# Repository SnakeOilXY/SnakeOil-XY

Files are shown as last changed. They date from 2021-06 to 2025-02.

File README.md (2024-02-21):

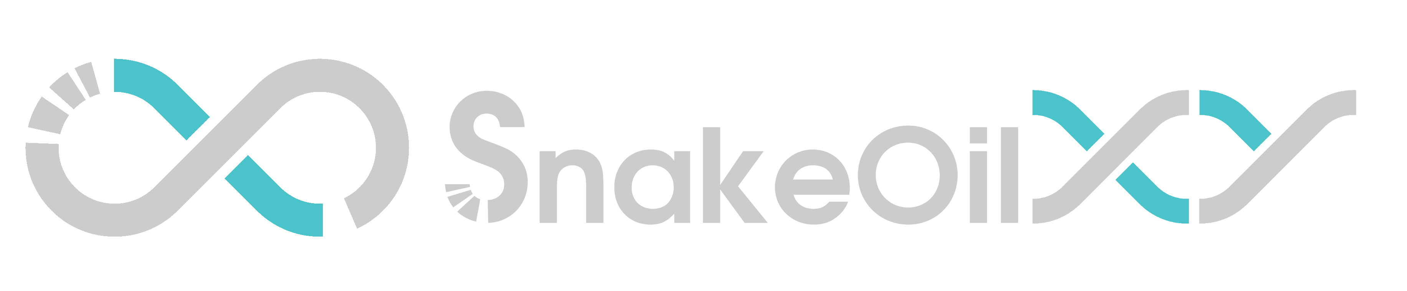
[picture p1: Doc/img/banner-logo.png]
Banner-logo


<a href="https://discord.gg/WZVP2HuAag" style="height: 40px !important;">Join us on Discord</a>

<a href='https://www.amazon.jp/hz/wishlist/ls/2AHXTCG01RYAZ?ref_=wl_share' target='_blank'>Buy Me a spool at amazon Japan</a>

# SnakeOil XY

Fully open source configurable high speed CoreXY 3D printer. Inspired by [HevORT](https://miragec79.github.io/HevORT/), [Voron](https://vorondesign.com/), [Annex Engineering](https://github.com/Annex-Engineering) and [EVA2](https://main.eva-3d.page/) design.

- Does not require any custom-machined parts or custom-cut panels.
- Can be selected one of the follwing kinematics.
    - Standard : Traditional corexy kinematic.
    - 4PR : High-performance machine with automatic squaring gantry capacity. This configuration uses custom [Extended CoreXY kinematic](https://github.com/SnakeOilXY/klipper-extended-corexy-kinematic) (Mixed cartesian and corexy).
    - IDEX : Hybrid corexy IDEX.
- CoreXY, IDEX, and Extended-CoreXY kinematics.
- Designed to last, parts under stress are embedded with long bolts to handle the load.
- And our industry-leading SnakeOil technology :3 

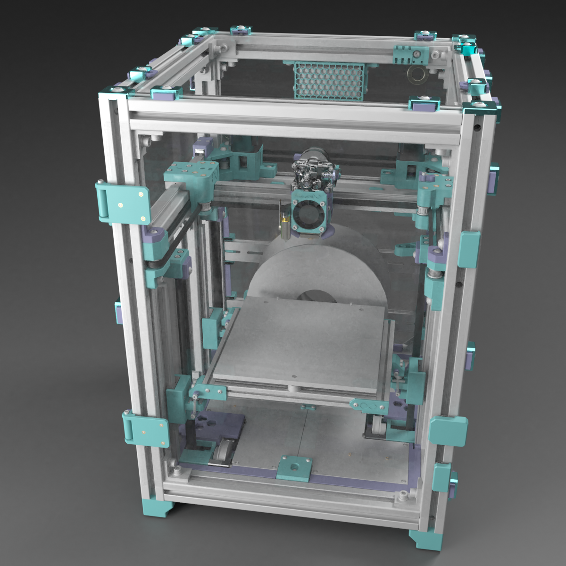
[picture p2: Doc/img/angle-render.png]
Render-angle


## Beta 3 release (2023-01-28)

- Add [IDEX variant](./BETA3_IDEX_Release_STL)(by Charles)
- Add [4PR variant](./BETA3_4PR_Release_STL) with new [Extended CoreXY kinematic](https://github.com/SnakeOilXY/klipper-extended-corexy-kinematic)
- Add klicky probe support(by Charles)
- New bed coupling kinematic using silicon spacers
- Add side-blower aux fan module
- Add EBB can toolhead board support
- Remove outdated components
- Merge toolhead design(1515 and 2020 gantry now use the same toolhead front/back/bottom design) and some small improvements on geometry

## Features

<table>
    <thead>
        <tr>
            <th>Feature</th>
            <th>Credit/Inspiration by/Description</th>
        </tr>
    </thead>
    <tbody>
        <tr>
            <td>Selectable kinematic : CoreXY, Hibryd-CoreXY </td>
            <td>Added on beta3 release</td>
        </tr>
        <tr>
            <td>Selectable single or dual toolhead </td>
            <td>Added on beta3 release</td>
        </tr>
        <tr>
            <td>3 Point auto bed tramming</td>
            <td>HevORT, Wobble ring</td>
        </tr>
        <tr>
            <td>Belted Z</td>
            <td>Lulz bot, Voron</td>
        </tr>
        <tr>
            <td>Din mounter</td>
            <td>Voron</td>
        </tr>
        <tr>
            <td>Cross belt corexy belt path</td>
            <td>HevORT</td>
        </tr>
        <tr>
            <td>Eva compatible toolhead</td>
            <td>EVA</td>
        </tr>
        <tr>
            <td>Filament spoll in side chamber</td>
            <td>-</td>
        </tr>
        <tr>
            <td>Quick release panels</td>
            <td>Added on beta2 release</td>
        </tr>
        <tr>
            <td>Built-in chamber air filter</td>
            <td>Added on beta1 release</td>
        </tr>
        <tr>
            <td>Auto build sheet detect and profile loader</td>
            <td>Work in progress</td>
        </tr>
        <tr>
            <td>AIO filament runout + jam detector + width sensor</td>
            <td>Work in progress</td>
        </tr>
        <tr>
            <td>Modular sensor add-on system</td>
            <td>Work in progress</td>
        </tr>
        <tr>
            <td>Probe(bed mesh) on print area only</td>
            <td>Added on beta2 using klipper macro</td>
        </tr>
        <tr>
            <td>Screwless belt mounter</td>
            <td>VzBot</td>
        </tr>
        <tr>
            <td>Bed fan</td>
            <td>Qholia</td>
        </tr>
    </tbody>
</table>

## Input shaper test result (beta2 1515 gantry with Sherpa mini extruder)

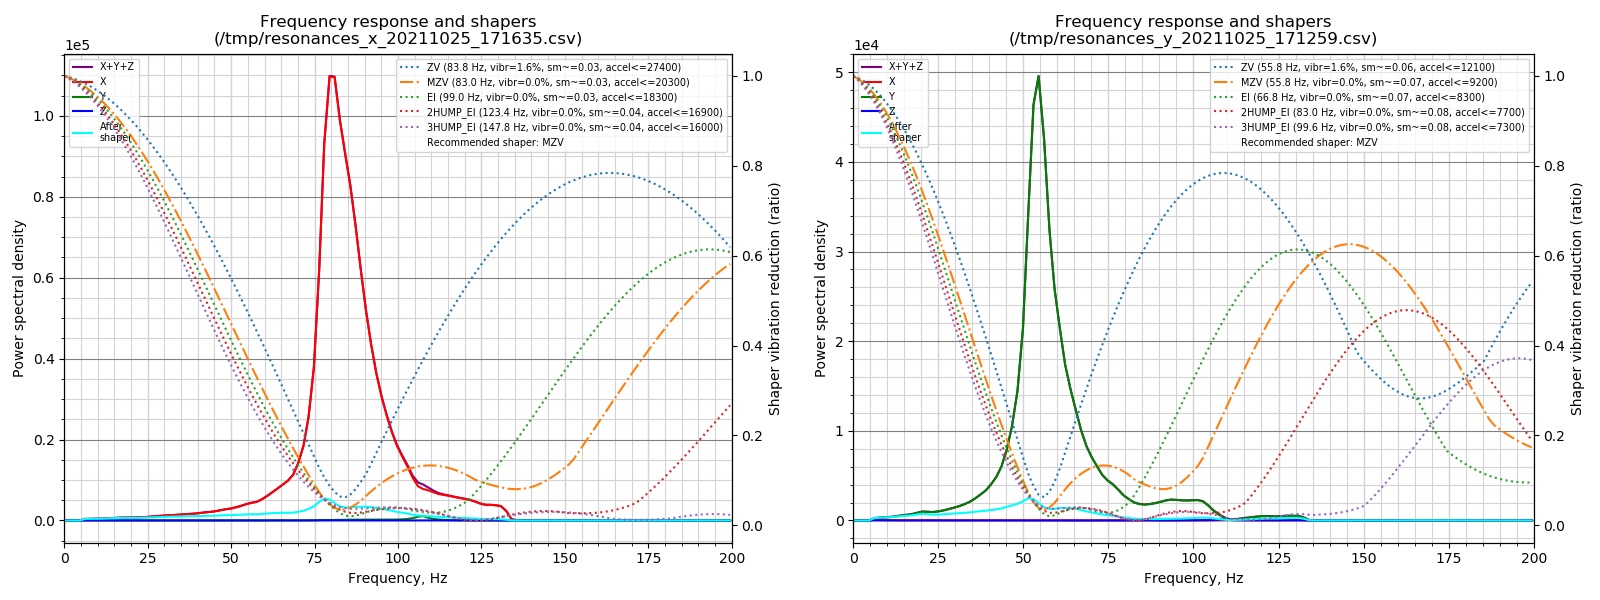
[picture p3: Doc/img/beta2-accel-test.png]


## Layer pitch measure (beta2 1515 gantry with Sherpa mini extruder)

- Measure result provided by [株式会社グーテンベルク](https://gutenberg.co.jp/)
- PLA, 0.4mm nozzle, sliced with Cura 4.12.1 using "CoreXY FAST" profile.

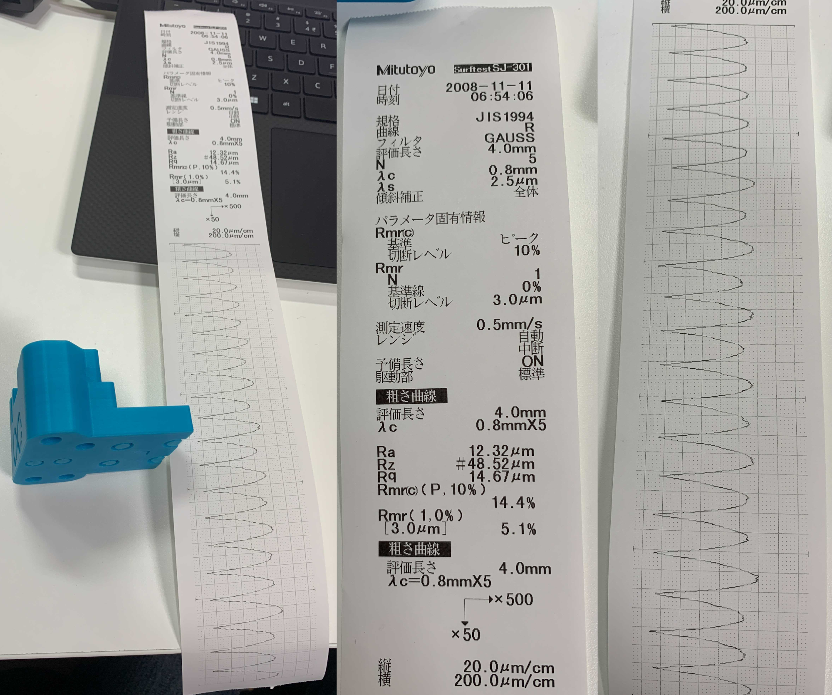
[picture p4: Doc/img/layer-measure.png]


## Demo videos

<table>
    <thead>
        <tr>
            <th></th>
            <th align="center">Bed coupling</th>
            <th align="center">SpeedBoatRace</th>
            <th align="center">Slow benchy</th>
        </tr>
    </thead>
    <tbody>
        <tr>
            <td>Video</td>
            <td align="center"><a href="https://youtu.be/pQPhEykthEg" rel="nofollow">
            Bed coupling</a></td>
            <td align="center"><a href="https://youtu.be/tPoP6zmxsCY" rel="nofollow">
            Speed benchy</a></td>
            <td align="center"><a href="https://youtu.be/kLawpgAUUPE" rel="nofollow">
            Speed benchy</a></td>
        </tr>
        <tr>
            <td>Hardware version</td>
            <td align="center">beta1</td>
            <td align="center">beta2</td>
            <td align="center">beta2</td>
        </tr>
    </tbody>
</table>

## BOM

## **_SnakeOil-XY currently has 2 versions_**

<code>Both machines are practicaly identical, only difference is the build volume. </code>

### 180x180x180mm build volume (Standard)

- [180<sup>3</sup>mm BOM](./Doc/BOM/bom-180.md)

### 250x240x230mm build volume (Large)

- [250<sup>3</sup>mm BOM](./Doc/BOM/bom-250.md)

## Manual

[>>> Click here <<<](./Doc/Manual/README.md)

## Firmware

[>>> Click here <<<](./Firmware/README.md)

## Copyright Notice

- [Sherpa mini extruder](https://github.com/Annex-Engineering/Sherpa_Mini-Extruder) is an original work of [Annex Engineering](https://github.com/Annex-Engineering), modified parts using their source code/design files are re-released under [ANNEX Engineering License](https://github.com/Annex-Engineering/ANNEX-Engineering-License-Agreement/blob/main/LICENSE.md).
- [EVA2](https://github.com/EVA-3D/eva-main) is an original work of [EVA-3D](https://github.com/EVA-3D), modified parts using their source code/design files are re-released under [GNU General Public License v3.0](https://github.com/EVA-3D/eva-main/blob/main/LICENSE)
- This printer design(SnakeOil XY), it's document and software are released under [GNU General Public License v3.0](https://github.com/ChipCE/SnakeOil-XY/blob/master/LICENSE)

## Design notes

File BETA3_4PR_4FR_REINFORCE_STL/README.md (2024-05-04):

# BETA3 Release - 4PR variant

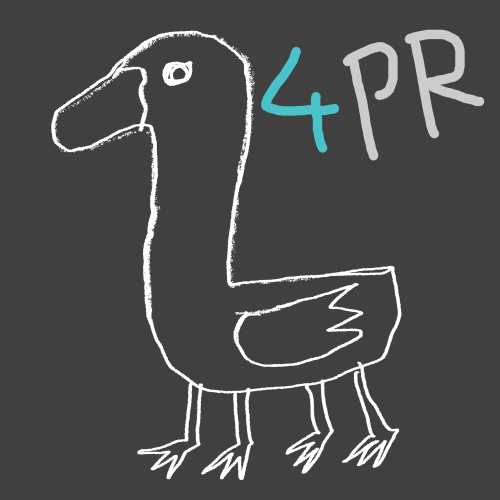
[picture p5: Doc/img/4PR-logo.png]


4PR(four paws runner) is an upgrade can add ontop of standard SnakeOilXY machines. This upgrade use our new kinematic called [Extended-corexy](https://github.com/SnakeOilXY/klipper-extended-corexy-kinematic). By adding two motors to assist the gantry on both ends, this upgrade greatly improves the performance of the existing CoreXY motion system.

## BOM

- WIP

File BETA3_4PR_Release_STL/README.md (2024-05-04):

# BETA3 Release - 4PR variant



4PR(four paws runner) is an upgrade can add ontop of standard SnakeOilXY machines. This upgrade use our new kinematic called [Extended-corexy](https://github.com/SnakeOilXY/klipper-extended-corexy-kinematic). By adding two motors to assist the gantry on both ends, this upgrade greatly improves the performance of the existing CoreXY motion system.

## BOM

<table>
    <thead>
        <tr>
            <th>Item</th>
            <th>Quantity</th>
            <th>Description</th>
            <th>default link/affiliate link</th>
            <th>non-affiliate link</th>
        </tr>
    </thead>
    <tbody>
        <tr>
            <td>M3x4-HeatSet</td>
            <td>12</td>
            <td>M3 X D4.2 X L4.0</td>
            <td><a href="https://s.click.aliexpress.com/e/_Ad1n92" rel="nofollow">Aliexpress</a></td>
            <td><a href="https://www.Aliexpress.com/item/1005002526998853.html" rel="nofollow">Aliexpress</a></td>
        </tr>
        <tr>
            <td>M4 hex nut</td>
            <td>2</td>
            <td></td>
            <td></td>
            <td></td>
        </tr>
        <tr>
            <td>Socket head M3x10</td>
            <td>8</td>
            <td>button head also works</td>
            <td>-</td>
            <td>-</td>
        </tr>
        <tr>
            <td>Socket head M3x25</td>
            <td>4</td>
            <td>button head also works</td>
            <td>-</td>
            <td>-</td>
        </tr>
        <tr>
            <td>Button head M3x12</td>
            <td>8</td>
            <td>-</td>
            <td>-</td>
            <td>-</td>
        </tr>
        <tr>
            <td>Button head M3x30</td>
            <td>8</td>
            <td>-</td>
            <td>-</td>
            <td>-</td>
        </tr>
        <tr>
            <td>Button head M5x25</td>
            <td>4</td>
            <td>-</td>
            <td>-</td>
            <td>-</td>
        </tr>
        <tr>
            <td>Button head M6x14</td>
            <td>6</td>
            <td>-</td>
            <td>-</td>
            <td>-</td>
        </tr>
        <tr>
            <td>Grub screw M5x20</td>
            <td>2</td>
            <td>-</td>
            <td>-</td>
            <td>-</td>
        </tr>
        <tr>
            <td>Nema 17 motor</td>
            <td>2</td>
            <td>Use the same type as AB motors.max length 48mm</td>
            <td>-</td>
            <td>-</td>
        </tr>
        <tr>
            <td>20T 6mm Pulley (5mm bore)</td>
            <td>2</td>
            <td>-</td>
            <td>-</td>
            <td><a href="https://www.Aliexpress.com/item/33023279793.html" rel="nofollow">Aliexpress</a></td>
        </tr>
        <tr>
            <td>20T 6mm Smooth Idler (5mm bore)</td>
            <td>2</td>
            <td>-</td>
            <td>-</td>
            <td><a href="https://www.Aliexpress.com/item/33023133633.html" rel="nofollow">Aliexpress</a></td>
        </tr>
        <tr>
            <td>20T 6mm Tooth Idler (5mm bore)</td>
            <td>4</td>
            <td>-</td>
            <td>-</td>
            <td><a href="https://www.Aliexpress.com/item/33023133633.html" rel="nofollow">Aliexpress</a></td>
        </tr>
        <tr>
            <td>MR115 bearing</td>
            <td>2</td>
            <td>-</td>
            <td>-</td>
            <td>-</td>
        </tr>
    </tbody>
</table>

## Other info

- comming soon

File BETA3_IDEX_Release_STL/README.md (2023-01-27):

# BETA2 Release(outdated document)

## What changed from Beta1

- Better 2020 gantry.
- New option for 1515 gantry with huge performance boost(see shaper test result below).
- New option for 1515 bed frame.
- New Z rail block mounting with limiter by default. This will keep the bed from tilting too much that cause the z probe cannot reach the bed.
- Better sherpa mini extruder mounter with 16mm shorter filament path.
- Added quick release front door and panel mounts.

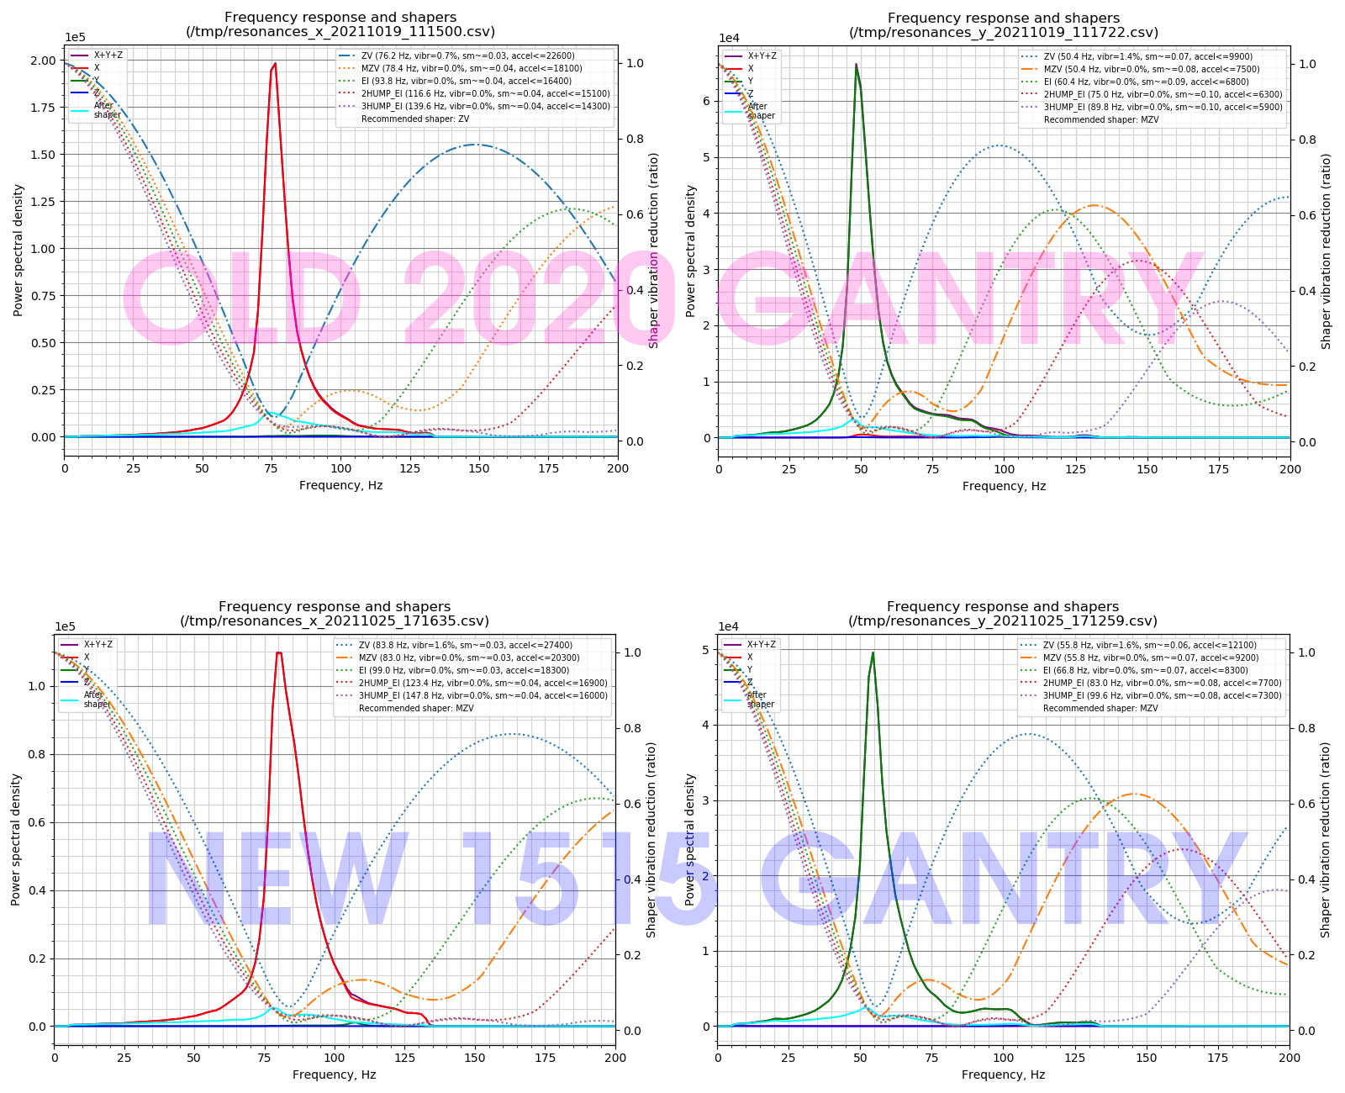
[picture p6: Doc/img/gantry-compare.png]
Banner


## What you need to reprint if you already have beta1 parts

- Z block mount
  - <code>1x_z-rail-block-mount-right-with-limiter.stl</code>
  - <code>2x_z-rail-block-mount-left-with-limiter.stl</code>
- Y carrier
  - <code>1x_y-carrier-bottom-left.stl</code>
  - <code>1x_y-carrier-bottom-right.stl</code>
  - <code>1x_y-carrier-top-left.stl</code>
  - <code>1x_y-carrier-top-right.stl</code>
- Extruder carrier parts
  - <code>1x_extruder-cable-support.stl</code>
  - <code>2x_extruder-belt-clamp.stl</code>
  - <code>2x_extruder-belt-tesioner.stl</code>
  - <code>1x_extruder-back-plate.stl</code>
  - <code>1x_extruder-front-plate.stl</code>
  - <code>And Sherpa mini mounter parts</code>

## What will be keep/change/added on later stable release

- Parts are tested and will not change on stable release
  - Motion system (XYZ) axis parts
  - Toolhead parts
  - Back and bottom panels/electronics mounter
- Parts are not tested, might change on later release
  - None
- Parts will be added later
  - Parts for 250mm3 machine size
  - Neopixel mount
  - Mounter to feed filament from outside enclosure
  - AIO filament sensor(jam/runout/fil.width detect)
  - Nozzle brush
- Parts will be replaced
  - None

## Parts printing

- Material : PETG, ABS, PC or anything you think will withstand the chamber temp you need.

- Recommended slicer setting:
  - Layer height : 0.2mm
  - Wall lines count : 5
  - Top/Bottom layers : 5
  - Infill : Gyroid 30%
  - Support placement : Touching d plate only

## Assembly, build help and bug report

- I don't have enough time to make the document atm. I will try to add document and build manual after finished design all the incomplete machine parts.
- For build log, help, and bug report please using [Our discord server](https://discord.gg/WZVP2HuAag)

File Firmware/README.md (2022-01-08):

# firmware

## Which firmware can be used

- Marlin
- Klipper
- RRF

## What does the board need that it can be used?

- 32bit
- 6 Stepper Motors or 5 Stepper + 1 Toolboard
- Neopixel Support
- 3 Thermistor Inputs (Hotend, Heated Bed, Enclosure)
- min 3 fan outputs

## Some Boards to choose from (incomplete list)

- Fysetc Spider
- BTT Octopus
- Mellow Fly Board
- BTT E3 RFF + IDEX
- BTT SKR Pro
- SKR 2.0 + BTT Mot Exp
- Duet 3 Mini 5+ + 2+ Addon or + Toolboard
- Duet 3
- Fysetc S6

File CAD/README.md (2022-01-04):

# CAD files

## FreeCAD source files

- You will need [FreeCAD](https://www.freecadweb.org/) and additional plugins to open the CAD file.
- After installed FreeCAD open menu <code>Tools</code> -> <code>Addon manager</code> then install <code>Assembly4</code> and <code>Fasteners</code> plugin.

## STEP

- There is no requirement to open STEP file, but the file is quite big and might take a long time to load

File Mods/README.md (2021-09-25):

# Some Mods for the SOXY
* GE5C Mod for the Bed (Voron Trident Inspired)

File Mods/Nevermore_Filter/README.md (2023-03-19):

# Nevermore Micro Mount for SnakeOil-XY

## Overview

This mod uses a custom plenum that mounts from the bottom (in stead of the side). I've been using it for roughly 100+ hours and have had zero issues so far. It's made a huge difference in the ABS fumes, and I also saw an increase in chamber temps by about ~5-7C.

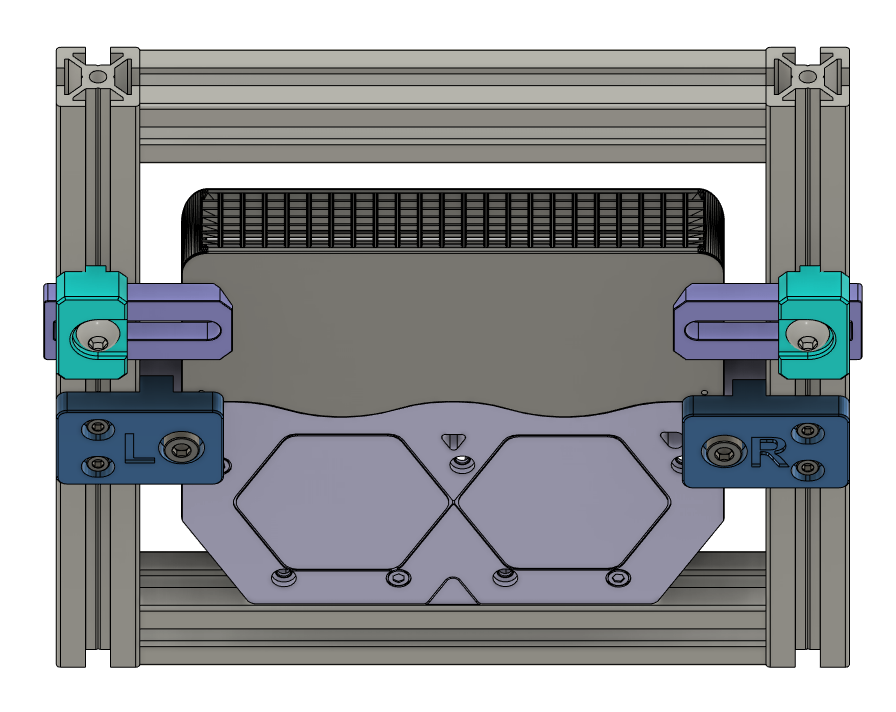
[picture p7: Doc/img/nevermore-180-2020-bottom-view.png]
Nevermore


Currently supports:
  - 180 size
    - 2020 bed - tested ✅
    - 1515 bed - untested ❓
  - 250 size 1515 bed - untested ❓
    - Can mount forward-facing, or sideways (potentially fitting 2x filters!)
  - IDEX 1515 bed - untested ❓
    - Easily fits 2x filters

## Printed parts

You will need to print the following parts:
  - **Custom Nevermore plenum**
    - Same for all sizes, except the 250 sideways mount for fitting 2x filters back-to-back
  - **Left and right mounts** inside their respective directories
  - **Center brace** (IDEX only)
  - **Nevermore cartridge**
    - You can use any Nevermore cartridge that you like, but I've supplied a custom cartridge that faces downward **and** uses the slide-in magnets. This worked the best for my use-case.
  - **[Optional] cartridge supports** to prevent cartridge from falling during printing (180 size 2020 bed only)
  - **[Optional] 1515 adapter** to support plenum against the back 1515 extrusion (originally designed to fit 2020 slot)

## BOM

In addition to the standard [Nevermore Micro BOM](https://github.com/nevermore3d/Nevermore_Micro#bom-v5), you will also need:

Fasteners (2020 bed)
  - 2x M5x7Dx7L heat set inserts
  - 2x M5x10mm socket head screws
  - 4x M3x8mm socket head screws
  - 4x M3 2020 T-nut
  - [optional] 1x M5x12mm button head screw and T-nut for each optional cartridge support arm

Fasteners (1515 bed)
  - 2x M5x7Dx7L heat set inserts
  - 2x M5x10mm socket head screws
  - 4x M3x12mm socket head screws
  - 4x M3 hex nut
  - [optional] 3x M3x6mm socket head screws (for rear 1515 support adapter)

Fasteners (IDEX 1515 bed 2x filters)
  - 2x M5x7Dx7L heat set inserts
  - 4x M5x10mm socket head screws
  - 4x M3x12mm socket head screws
  - 4x M3 hex nut

See each directory for more info.

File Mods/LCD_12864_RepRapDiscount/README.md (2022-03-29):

# RepRapDiscount Full Graphic Smart Controller (128x64 ST7920)

This type of LCD screen is often used in older Chinese 3D printers. This model would be useful for those who cannibalize old printers to build SnakeOil-XY. Silkscreen reads like: "RepRapDiscount Full Graphic Smart Controller www.bigtree-tech.com".

LCD controller: ST7920

[printer.cfg sample](sample-printer-cfg.cfg) - you can replace the latter part with the pin arrangement of your MCU.

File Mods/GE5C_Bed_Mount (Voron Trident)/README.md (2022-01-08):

# WORK IN PROGRESS
## Not tested Yet

BOM (different from the mainline repo)

* 9x M3x6 DIN 7380 Screw
* 6x M5x16 DIN 7380 Screw
* 3x M5 Nut
* 3x GE5C Bearing or IGUS EGLM-05

The Nut has to be inserted while printing via a Pause command.

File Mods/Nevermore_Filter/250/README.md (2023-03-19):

# Nevermore mount for SnakeOil-XY 250 **(UNTESTED)**

There are two options for the 250 version
- Forward-facing 
- Sideways-facing, which potentially allows for installing two filters

The STEP file includes both versions (one of them mirrored)

## Forward-facing **(UNTESTED)**
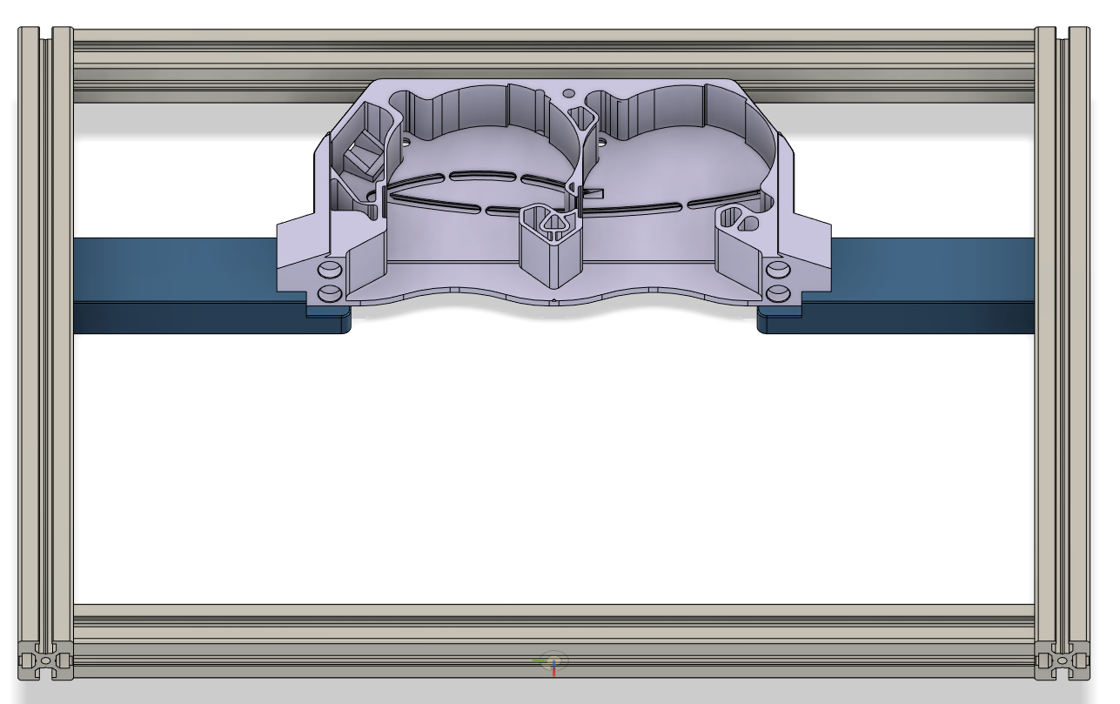
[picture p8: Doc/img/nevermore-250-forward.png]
nevermore-250-forward


I've also included and optional 1515 plenum support adapter (forward-facing only), but it may not be necessary.

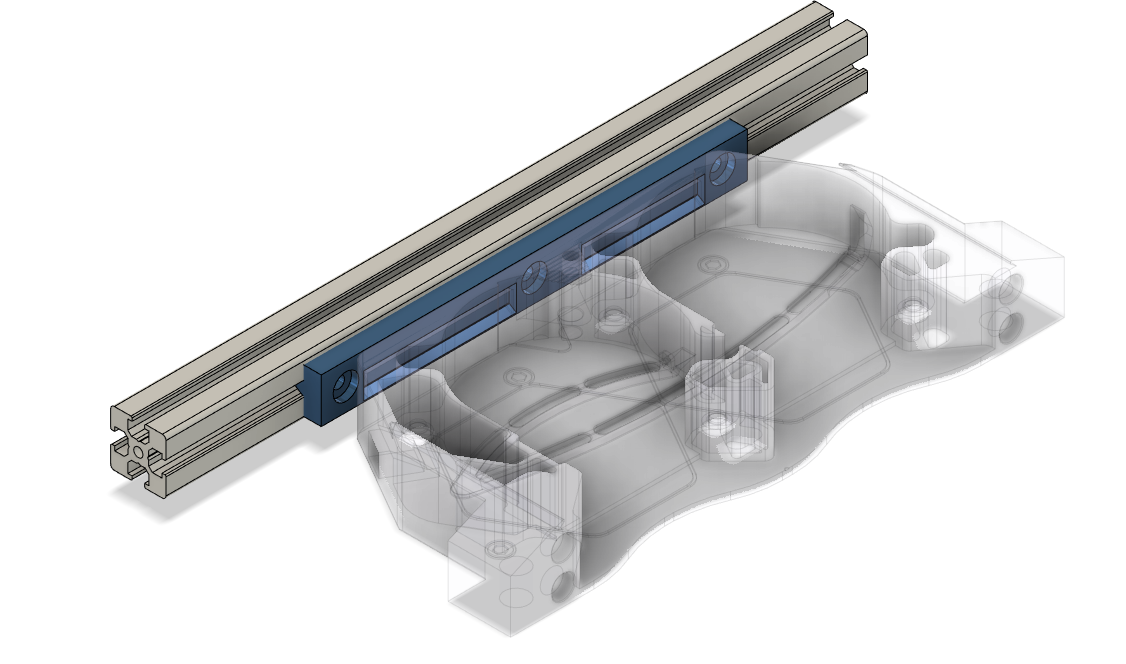
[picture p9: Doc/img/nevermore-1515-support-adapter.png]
nevermore-1515-support-adapter


## Sideways-facing (optional 2x filters) **(UNTESTED)**
- Note that Plenum's rear support is cut off in this version to provide clearance for the back-to-back-filters.

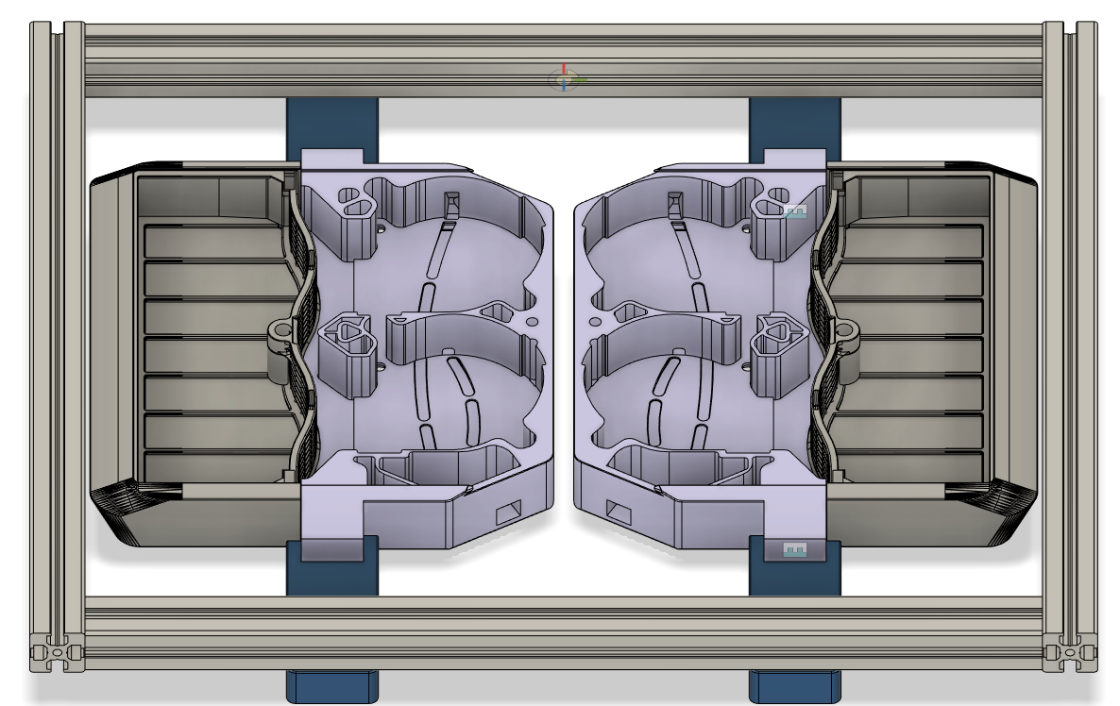
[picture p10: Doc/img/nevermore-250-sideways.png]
nevermore-250-sideways


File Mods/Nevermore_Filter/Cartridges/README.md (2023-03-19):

# Preferred Nevermore Cartridges for SnakeOil-XY

The [V18_cartridge_RC2.stl](
https://github.com/nevermore3d/Nevermore_Micro/blob/4df5884a6275a27d29d09b3c8c44b67c10dba5ab/V5_Duo/1.8/V18_cartridge_RC2.stl) from the official Nevermore repository is a great option, as it blows the air at a slightly downward angle.

However, my magnets kept falling out so I combined the above file with ChainsDD's [slide-in magnets mod](https://github.com/nevermore3d/Nevermore_Micro/tree/4df5884a6275a27d29d09b3c8c44b67c10dba5ab/V5_Duo/Mods/Slide-in-Magnets_by-ChainsDD).

The magnets are slightly weaker when behind the plastic, so you will most likely need some kind of support for the cartridge if you use this version.

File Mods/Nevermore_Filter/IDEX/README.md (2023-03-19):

# Nevermore mount for SnakeOil-XY IDEX **(UNTESTED)**

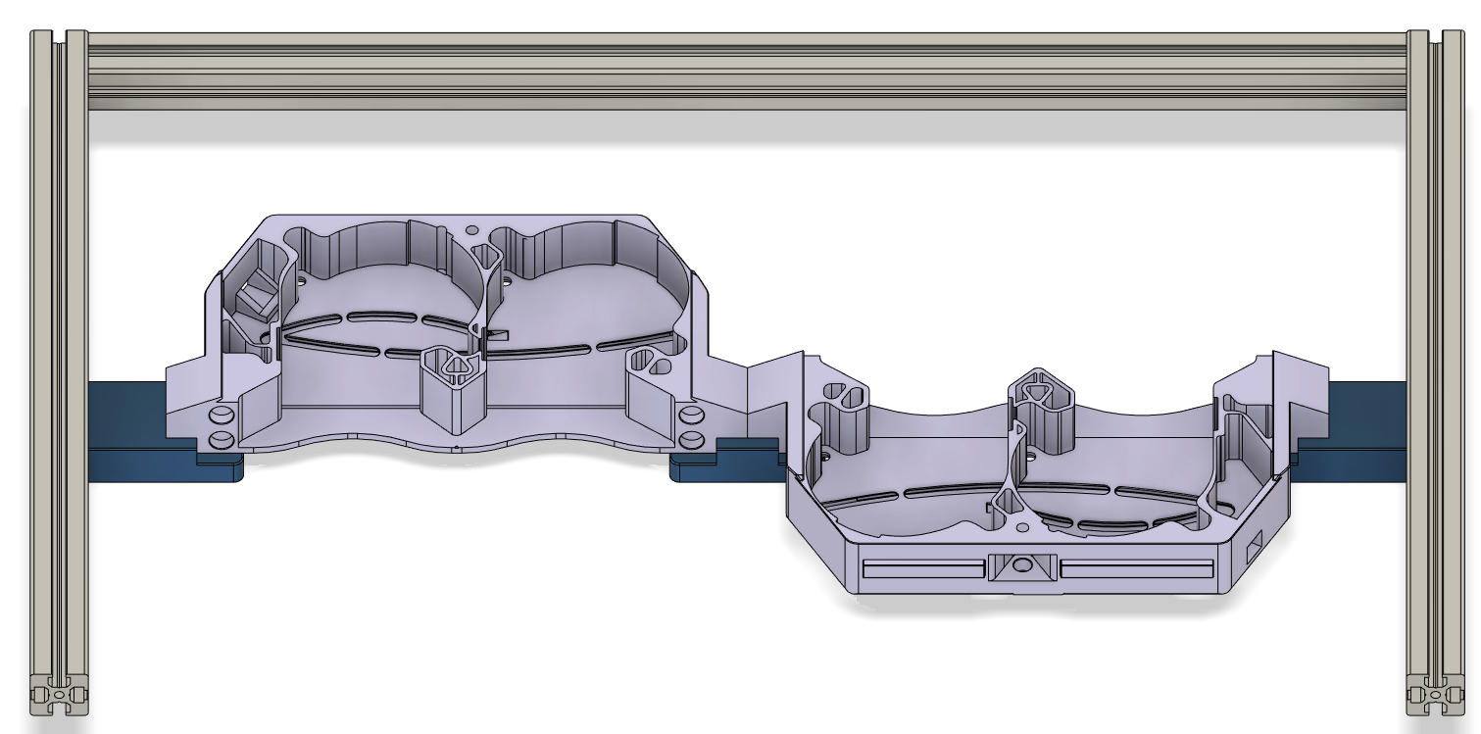
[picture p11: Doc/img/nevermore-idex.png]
nevermore-idex


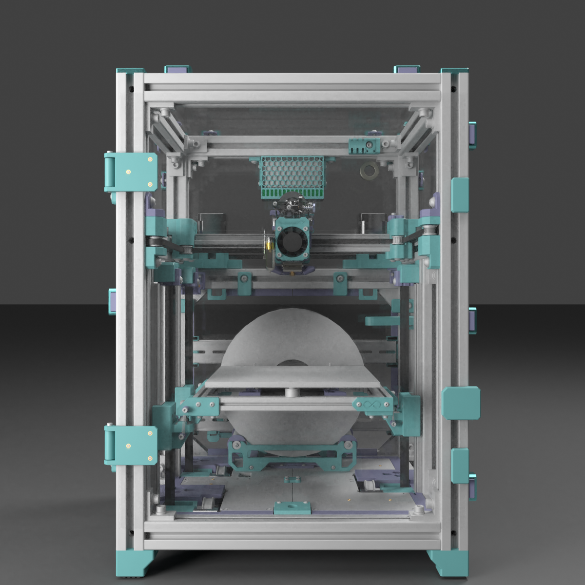
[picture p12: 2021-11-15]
Doc/img/front-render.png

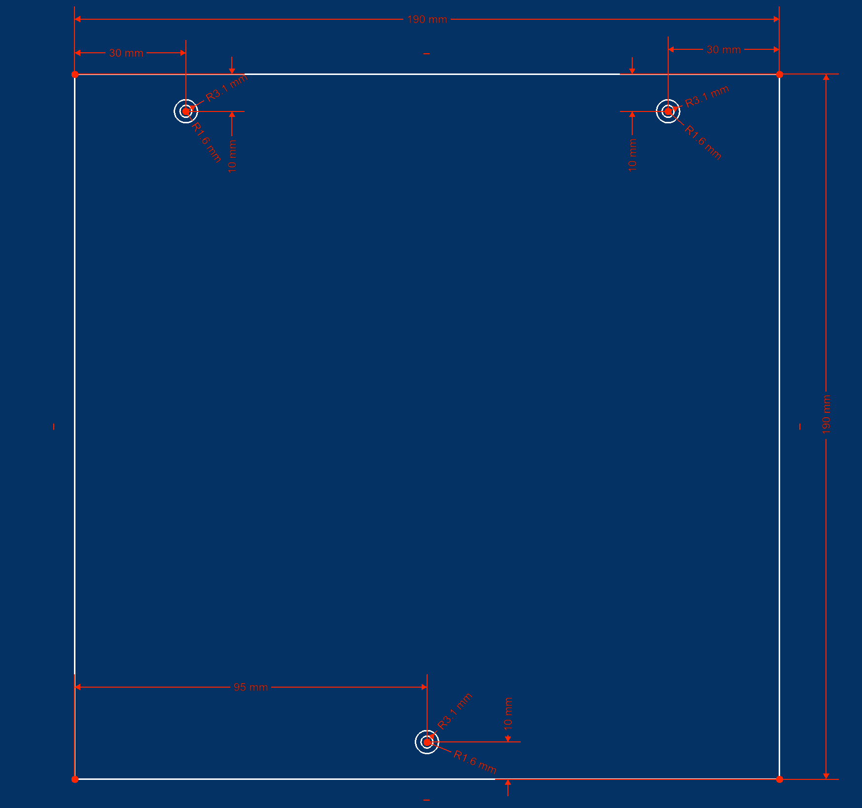
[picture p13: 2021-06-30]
Doc/img/190x190-bed.png

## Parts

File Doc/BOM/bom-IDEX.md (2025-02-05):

#IDEX 250mm BOM

<code>Status : work in progress</code>  
<code>Last updated : 2022-08-31</code>

<code> Fell free to [contact me](https://discord.gg/WZVP2HuAag) if you spot mistake or have question.</code>

## Read this first

## Table of contents

- [0.Kit](#0kit)
- [1.Frame](#1frame)
  - [Main Frame](#main-frame)
  - [Bed](#bed)
    - [1515 profile (recommended)](#1515-profile-recommended)
    - [2020 profile](#2020-profile)
  - [Gantry](#gantry)
    - [1515 profile (recommended)](#1515-profile-recommended-1)
    - [2020 profile](#2020-profile-1)
- [2.Fasteners](#2fasteners)
  - [Nuts and bolt](#nuts-and-bolt)
- [3.Motion](#3motion)
- [4. Electronics](#4-electronics)
- [5.Panels](#5panels)
- [6.Other](#6other)
- [7.Alternative bed coupling options](#7alternative-bed-coupling-options)
- [8.Z counter weight](#8z-counter-weight)

# 0.Kit

Some parts listed on the BOM can be purchased in kit format from below vendors

- [kb-3d.com store](https://kb-3d.com/store/81-snakeoilxy)

# 1.Frame

- [Main Frame](#main-frame)
- [Bed](#bed)
- [Gantry](#gantry)

## Main Frame

<table>
    <thead>
        <tr>
            <th>Item</th>
            <th>Quantity</th>
            <th>Misumi code</th>
        </tr>
    </thead>
	  <tbody>
        <tr>
            <td>3030 Extrusion 330mm</td>
            <td>3</td>
            <td>HFS6-3030-330</td>
        </tr>
        <tr>
            <td>3030 Extrusion 550mm</td>
            <td>4</td>
            <td>HFS6-3030-550</td>
        </tr>
        <tr>
            <td>3030 Extrusion 460mm</td>
            <td>5</td>
            <td>HFS6-3030-380</td>
        </tr>
        <tr>
            <td>3030 Extrusion 360mm</td>
            <td>6</td>
            <td>HFS6-3030-360</td>
        </tr>
        <tr>
            <td>3030, 30mm long, 20mm thick corner bracket<br>
            <a href="./corner-brackets.md" rel="nofollow">Check this if you don't have access to misumi brackets</a></td>
            <td>29</td>
            <td>HBLFSN6</td>
        </tr>
    </tbody>
</table>

<code>3030 extrusions are 8mm slot type, 2020 extrusions are 6mm slot type, 1515 extrusions are 3.4mm slot type
</code>

## Bed

### 1515 profile (recommended)

Instead of 1515 profile you can use [MakerBeamXL](https://www.makerbeam.com/makerbeamxl/), you just need to print a different version of the mountings.

<table>
    <thead>
        <tr>
            <th>Item</th>
            <th>Quantity</th>
            <th>Misumi code</th>
        </tr>
    </thead>
	  <tbody>
        <tr>
            <td>1515 Extrusion 340mm</td>
            <td>2</td>
            <td>HFS3-1515-340</td>
        </tr>
        <tr>
            <td>1515 Extrusion 235mm</td>
            <td>2</td>
            <td>HFS3-1515-235</td>
        </tr>
        <tr>
            <td>1515 Corner bracket</td>
            <td>4</td>
            <td>HBLTBS3</td>
        </tr>
    </tbody>
</table>

### 2020 profile

<table>
    <thead>
        <tr>
            <th>Item</th>
            <th>Quantity</th>
            <th>Misumi code</th>
        </tr>
    </thead>
	  <tbody>
        <tr>
            <td>2020 Extrusion 320mm</td>
            <td>2</td>
            <td>HFS5-2020-320</td>
        </tr>
        <tr>
            <td>2020 Extrusion 220mm</td>
            <td>2</td>
            <td>HFS5-2020-220</td>
        </tr>
        <tr>
            <td>2020 Corner bracket</td>
            <td>4</td>
            <td>HBLSS5</td>
        </tr>
    </tbody>
</table>

## Gantry

### 1515 profile (recommended)

Instead of 1515 profile you can use [MakerBeamXL](https://www.makerbeam.com/makerbeamxl/), you just need to print a different version of the mountings.

<table>
    <thead>
        <tr>
            <th>Item</th>
            <th>Quantity</th>
            <th>Misumi code</th>
        </tr>
    </thead>
	  <tbody>
        <tr>
            <td>1515 Extrusion 440mm</td>
            <td>1</td>
            <td>HFS3-1515-440</td>
        </tr>
    </tbody>
</table>

### 2020 profile

<table>
    <thead>
        <tr>
            <th>Item</th>
            <th>Quantity</th>
            <th>Misumi code</th>
        </tr>
    </thead>
	  <tbody>
        <tr>
            <td>2020 Extrusion 440mm</td>
            <td>1</td>
            <td>HFS5-2020-440</td>
        </tr>
    </tbody>
</table>

# 2.Fasteners

## Nuts and bolt

<table>
    <thead>
        <tr>
            <th>Item</th>
            <th>Quantity</th>
            <th>Description</th>
            <th>default link/affiliate link</th>
            <th>non-affiliate link</th>
        </tr>
    </thead>
    <tbody>
        <tr>
            <td>2020 M3 T-nut</td>
            <td>20</td>
            <td>for 2020 bed frame and gantry</td>
            <td><a href="https://s.click.aliexpress.com/e/_ASabWc" rel="nofollow">Aliexpress</a></td>
            <td><a href="https://www.aliexpress.com/item/4000293743251.html" rel="nofollow">Aliexpress</a></td>
        </tr>
        <tr>
            <td>2020 M5 T-nut</td>
            <td>15</td>
            <td> for 2020 bed frame and gantry</td>
            <td><a href="https://s.click.aliexpress.com/e/_ASabWc" rel="nofollow">Aliexpress</a></td>
            <td><a href="https://www.aliexpress.com/item/4000293743251.html" rel="nofollow">Aliexpress</a></td>
        </tr>
        <tr>
            <td>Square nut M3(hex nut also works)</td>
            <td>30</td>
            <td> for 1515 bed frame and gantry</td>
            <td></td>
            <td></td>
        </tr>
        <tr>
            <td>3030 M3 T-nut</td>
            <td>60</td>
            <td></td>
            <td><a href="https://s.click.aliexpress.com/e/_ASabWc" rel="nofollow">Aliexpress</a></td>
            <td><a href="https://www.aliexpress.com/item/4000293743251.html" rel="nofollow">Aliexpress</a></td>
        </tr>
        <tr>
            <td>3030 M5 T-nut</td>
            <td>10</td>
            <td></td>
            <td><a href="https://s.click.aliexpress.com/e/_ASabWc" rel="nofollow">Aliexpress</a></td>
            <td><a href="https://www.aliexpress.com/item/4000293743251.html" rel="nofollow">Aliexpress</a></td>
        </tr>
        <tr>
            <td>3030 M6 T-nut</td>
            <td>160</td>
            <td></td>
            <td><a href="https://s.click.aliexpress.com/e/_ASabWc" rel="nofollow">Aliexpress</a></td>
            <td><a href="https://www.aliexpress.com/item/4000293743251.html" rel="nofollow">Aliexpress</a></td>
        </tr>
    </tbody>
</table>

<table>
    <thead>
        <tr>
            <th>Item</th>
            <th>Quantity</th>
            <th>Description</th>
            <th>default link/affiliate link</th>
            <th>non-affiliate link</th>
        </tr>
    </thead>
    <tbody>
        <tr>
            <td>M3x3-HeatSet</td>
            <td>50</td>
            <td>M3 X D4.2 X L3.0</td>
            <td><a href="https://s.click.aliexpress.com/e/_Ad1n92" rel="nofollow">Aliexpress</a></td>
            <td><a href="https://www.Aliexpress.com/item/1005002526998853.html" rel="nofollow">Aliexpress</a></td>
        </tr>
        <tr>
            <td>M3x4-HeatSet</td>
            <td>150</td>
            <td>M3 X D4.2 X L4.0</td>
            <td><a href="https://s.click.aliexpress.com/e/_Ad1n92" rel="nofollow">Aliexpress</a></td>
            <td><a href="https://www.Aliexpress.com/item/1005002526998853.html" rel="nofollow">Aliexpress</a></td>
        </tr>
        <tr>
            <td>M3x5x4-HeatSet</td>
            <td>5</td>
            <td>M3 X D5.0 X L4.0 (for sherpa mini)</td>
            <td><a href="https://s.click.aliexpress.com/e/_AcLT3I" rel="nofollow">Aliexpress</a></td>
            <td><a href="https://www.aliexpress.com/item/4000232858343.html" rel="nofollow">Aliexpress</a></td>
        </tr>
        <tr>
            <td>M4-HeatSet</td>
            <td>3</td>
            <td>M4 X D6.0 X L4.0 (for threaded ball bed coupler)</td>
            <td><a href="https://s.click.aliexpress.com/e/_A9WsSs" rel="nofollow">Aliexpress</a></td>
            <td><a href="https://www.Aliexpress.com/item/4000232925592.html" rel="nofollow">Aliexpress</a></td>
        </tr>
        <tr>
            <td>M5-HeatSet</td>
            <td>10</td>
            <td>M5 X D7.0 X L7.0</td>
            <td><a href="https://s.click.aliexpress.com/e/_AZBpZE" rel="nofollow">Aliexpress</a></td>
            <td><a href="https://www.aliexpress.com/item/4000232990523.html" rel="nofollow">Aliexpress</a></td>
        </tr>
    </tbody>
</table>

<table>
    <thead>
        <tr>
            <td>Item</td>
            <td>Quantity</td>
            <td>Description</td>
            <td>Norm</td>
        </tr>
    </thead>
    <tbody>
        <tr>
            <td>Button head M3x6</td>
            <td>75</td>
            <td></td>
            <td>ISO 7380 / DIN 7380</td>
        </tr>
        <tr>
            <td>Button head M3x8</td>
            <td>3</td>
            <td></td>
            <td>ISO 7380 / DIN 7380</td>
        </tr>
        <tr>
            <td>Button head M3x10</td>
            <td>14</td>
            <td></td>
            <td>ISO 7380 / DIN 7380</td>
        </tr>
        <tr>
            <td>Button head M3x12</td>
            <td>10</td>
            <td></td>
            <td>ISO 7380 / DIN 7380</td>
        </tr>
        <tr>
            <td>Button head M3x16</td>
            <td>5</td>
            <td></td>
            <td>ISO 7380 / DIN 7380</td>
        </tr>
        <tr>
            <td>Button head M3x20</td>
            <td>1</td>
            <td></td>
            <td>ISO 7380 / DIN 7380</td>
        </tr>
        <tr>
            <td>Button head M3x30</td>
            <td>4</td>
            <td></td>
            <td>ISO 7380 / DIN 7380</td>
        </tr>
        <tr>
            <td>Button head M3x35</td>
            <td>2</td>
            <td></td>
            <td>ISO 7380 / DIN 7380</td>
        </tr>
        <tr>
            <td>Button head M4x6</td>
            <td>4</td>
            <td></td>
            <td>ISO 7380 / DIN 7380</td>
        </tr>
        <tr>
            <td>Button head M4x25</td>
            <td>2</td>
            <td></td>
            <td>ISO 7380 / DIN 7380</td>
        </tr>
        <tr>
            <td>Button head M5x10</td>
            <td>6</td>
            <td></td>
            <td>ISO 7380 / DIN 7380</td>
        </tr>
        <tr>
            <td>Button head M5x25</td>
            <td>3</td>
            <td></td>
            <td>ISO 7380 / DIN 7380</td>
        </tr>
        <tr>
            <td>Button head M5x40</td>
            <td>5</td>
            <td></td>
            <td>ISO 7380 / DIN 7380</td>
        </tr>
        <tr>
            <td>Button head M5x45</td>
            <td>1</td>
            <td></td>
            <td>ISO 7380 / DIN 7380</td>
        </tr>
        <tr>
            <td>Button head M5x50</td>
            <td>8</td>
            <td></td>
            <td>ISO 7380 / DIN 7380</td>
        </tr>
        <tr>
            <td>Button head M6x10</td>
            <td>17</td>
            <td></td>
            <td>ISO 7380 / DIN 7380</td>
        </tr>
        <tr>
            <td>Button head M6x12</td>
            <td>10</td>
            <td></td>
            <td>ISO 7380 / DIN 7380</td>
        </tr>
        <tr>
            <td>Button head M6x14</td>
            <td>17</td>
            <td></td>
            <td>ISO 7380 / DIN 7380</td>
        </tr>
        <tr>
            <td>Button head M6x16</td>
            <td>48</td>
            <td></td>
            <td>ISO 7380 / DIN 7380</td>
        </tr>
        <tr>
            <td>Button head M6x20</td>
            <td>4</td>
            <td></td>
            <td>ISO 7380 / DIN 7380</td>
        </tr>
        <tr>
            <td>Button head M6x25</td>
            <td>1</td>
            <td></td>
            <td>ISO 7380 / DIN 7380</td>
        </tr>
        <tr>
            <td>Button head M6x35</td>
            <td>6</td>
            <td></td>
            <td>ISO 7380 / DIN 7380</td>
        </tr>
        <tr>
            <td>Button head M8x12</td>
            <td>4</td>
            <td></td>
            <td>ISO 7380 / DIN 7380</td>
        </tr>
        <tr>
            <td>Button head M8x20</td>
            <td>30</td>
			<td>Only needed 8 if you buy HCJ_Joint.</br> The other 22 M8x20 bolts will be included in HCJ joint set</td>
            <td>ISO 7380 / DIN 7380</td>
        </tr>
    </tbody>
</table>

<table>
    <thead>
        <tr>
            <td>Item</td>
            <td>Quantity</td>
            <td>Description</td>
            <td>Norm</td>
        </tr>
    </thead>
    <tbody>
        <tr>
            <td>Socket head M2.5x12</td>
            <td>2</td>
            <td></td>
            <td>DIN 912 / ISO 4762</td>
        </tr>
        <tr>
            <td>Socket head M3x6</td>
            <td>6</td>
            <td></td>
            <td>DIN 912 / ISO 4762</td>
        </tr>
        <tr>
            <td>Socket head M3x8</td>
            <td>57</td>
            <td></td>
            <td>DIN 912 / ISO 4762</td>
        </tr>
        <tr>
            <td>Socket head M3x10</td>
            <td>107</td>
            <td></td>
            <td>DIN 912 / ISO 4762</td>
        </tr>
        <tr>
            <td>Socket head M3x12</td>
            <td>18</td>
            <td></td>
            <td>DIN 912 / ISO 4762</td>
        </tr>
        <tr>
            <td>Socket head M3x14</td>
            <td>18</td>
            <td></td>
            <td>DIN 912 / ISO 4762</td>
        </tr>
        <tr>
            <td>Socket head M3x16</td>
            <td>10</td>
            <td></td>
            <td>DIN 912 / ISO 4762</td>
        </tr>
        <tr>
            <td>Socket head M3x20</td>
            <td>3</td>
            <td></td>
            <td>DIN 912 / ISO 4762</td>
        </tr>
        <tr>
            <td>Socket head M3x25</td>
            <td>8</td>
            <td></td>
            <td>DIN 912 / ISO 4762</td>
        </tr>
        <tr>
            <td>Socket head M3x35</td>
            <td>9</td>
            <td></td>
            <td>DIN 912 / ISO 4762</td>
        </tr>
        <tr>
            <td>Socket head M3x40</td>
            <td>15</td>
            <td></td>
            <td>DIN 912 / ISO 4762</td>
        </tr>
        <tr>
            <td>Socket head M3x45</td>
            <td>3</td>
            <td></td>
            <td>DIN 912 / ISO 4762</td>
        </tr>
        <tr>
            <td>Socket head M3x70</td>
            <td>6</td>
            <td></td>
            <td>DIN 912 / ISO 4762</td>
        </tr>
        <tr>
            <td>Socket head M6x14</td>
            <td>56</td>
            <td></td>
            <td>DIN 912 / ISO 4762</td>
        </tr>
    </tbody>
</table>

<table>
    <thead>
        <tr>
            <td>Item</td>
            <td>Quantity</td>
            <td>Description</td>
            <td>Norm</td>
        </tr>
    </thead>
    <tbody>
        <tr>
            <td>Grub M3x8</td>
            <td>5</td>
            <td></td>
            <td>DIN 913 / ISO 4026</td>
        </tr>
        <tr>
            <td>Grub M4x12</td>
            <td>3</td>
            <td>(for threaded ball bed coupler)</td>
            <td>DIN 913 / ISO 4026</td>
        </tr>
        <tr>
            <td>Self taping screw M2x10</td>
            <td>4</td>
            <td></td>
            <td>-</td>
        </tr>
    </tbody>
</table>

<table>
    <thead>
        <tr>
            <td>Item</td>
            <td>Quantity</td>
            <td>Description</td>
            <td>Norm</td>
        </tr>
    </thead>
    <tbody>
        <tr>
            <td>Hex M3 nut</td>
            <td>8</td>
            <td></td>
            <td>DIN 934 / ISO 4032</td>
        </tr>
        <tr>
            <td>Hex M4 nut</td>
            <td>2</td>
            <td></td>
            <td>DIN 934 / ISO 4032</td>
        </tr>
        <tr>
            <td>Hex M5 nut</td>
            <td>4</td>
            <td></td>
            <td>DIN 934 / ISO 4032</td>
        </tr>
    </tbody>
</table>

<table>
    <thead>
        <tr>
            <td>Item</td>
            <td>Quantity</td>
            <td>Description</td>
            <td>Norm</td>
        </tr>
    </thead>
    <tbody>
        <tr>
            <td>Small M3 washer</td>
            <td>71</td>
            <td></td>
            <td>ISO 7092 / DIN 433</td>
        </tr>
        <tr>
            <td>Small M5 washer</td>
            <td>2</td>
            <td></td>
            <td>ISO 7092 / DIN 433</td>
        </tr>
        <tr>
            <td>Normal M5 washer</td>
            <td>4*</td>
            <td>Check out a few lines below </td>
            <td>DIN 125 / ISO 7089</td>
        </tr>
        <tr>
            <td>Normal M6 washer</td>
            <td>91*</td>
            <td>Check out a few lines below </td>
            <td>DIN 125 / ISO 7089</td>
        </tr>
        <tr>
            <td>Wide M3 washer</td>
            <td>16</td>
            <td></td>
            <td>DIN 9021 / ISO 7093</td>
        </tr>
        <tr>
            <td>Spring M3 washer </td>
            <td>60</td>
            <td></td>
            <td>DIN 127 </td>
        </tr>
        <tr>
            <td>Normal M3 washer</td>
            <td>370</td>
            <td>We don't have a simple way to calculate the amount of washers you will need, if your budget can afford it buy as many as bolts </td>
            <td>DIN 125 / ISO 7089</td>
        </tr>
        <tr>
            <td>Normal M4 washer</td>
            <td>6</td>
            <td>We don't have a simple way to calculate the amount of washers you will need, if your budget can afford it buy as many as bolts </td>
            <td>DIN 125 / ISO 7089</td>
        </tr>
        <tr>
            <td>Normal M5 washer</td>
            <td>23</td>
            <td>We don't have a simple way to calculate the amount of washers you will need, if your budget can afford it buy as many as bolts </td>
            <td>DIN 125 / ISO 7089</td>
        </tr>
        <tr>
            <td>Normal M6 washer</td>
            <td>159</td>
            <td>We don't have a simple way to calculate the amount of washers you will need, if your budget can afford it buy as many as bolts </td>
            <td>DIN 125 / ISO 7089</td>
        </tr>
    </tbody>
</table>

# 3.Motion

<table>
    <thead>
        <tr>
            <th>Item</th>
            <th>Quantity</th>
            <th>Description</th>
            <th>default link/affiliate link</th>
            <th>non-affiliate link</th>
        </tr>
    </thead>
    <tbody>
        <tr>
            <td>MGN12H 300mm</td>
            <td>5</td>
            <td></td>
            <td></td>
            <td><a href="https://www.aliexpress.com/item/32829826159.html" rel="nofollow">Aliexpress</a></td>
        </tr>
        <tr>
            <td>MGN12H 400mm</td>
            <td>1</td>
            <td></td>
            <td></td>
            <td><a href="https://www.aliexpress.com/item/32829826159.html" rel="nofollow">Aliexpress</a></td>
        </tr>
        <tr>
            <td>20T 6mm Pulley (5mm bore)</td>
            <td>4</td>
            <td></td>
            <td></td>
            <td><a href="https://www.Aliexpress.com/item/33023279793.html" rel="nofollow">Aliexpress</a></td>
        </tr>
        <tr>
            <td>16T 6mm Pulley (5mm bore)</td>
            <td>3</td>
            <td></td>
            <td></td>
            <td><a href="https://www.Aliexpress.com/item/33002989677.html" rel="nofollow">Aliexpress</a></td>
        </tr>
        <tr>
            <td>80T 6mm Pulley (5mm bore)</td>
            <td>3</td>
            <td></td>
            <td></td>
            <td><a href="https://www.Aliexpress.com/item/1005001700640216.html" rel="nofollow">Aliexpress</a></td>
        </tr>
        <tr>
            <td>20T 9mm Pulley (5mm bore)</td>
            <td>3</td>
            <td></td>
            <td></td>
            <td><a href="https://www.Aliexpress.com/item/33023279793.html" rel="nofollow">Aliexpress</a></td>
        </tr>
        <tr>
            <td>20T 6mm Smooth Idler (5mm bore)</td>
            <td>12</td>
            <td></td>
            <td></td>
            <td><a href="https://www.Aliexpress.com/item/33023133633.html" rel="nofollow">Aliexpress</a></td>
        </tr>
        <tr>
            <td>20T 6mm Tooth Idler (5mm bore)</td>
            <td>6</td>
            <td></td>
            <td></td>
            <td><a href="https://www.Aliexpress.com/item/33023133633.html" rel="nofollow">Aliexpress</a></td>
        </tr>
        <tr>
            <td>20T 9mm Tooth idler (5mm bore)</td>
            <td>3</td>
            <td></td>
            <td></td>
            <td><a href="https://www.Aliexpress.com/item/33023133633.html" rel="nofollow">Aliexpress</a></td>
        </tr>
        <tr>
            <td>Close loop 188-2GT-6 RF belt</td>
            <td>3</td>
            <td></td>
            <td></td>
            <td><a href="https://www.Aliexpress.com/item/4000397043382.html" rel="nofollow">Aliexpress</a></td>
        </tr>
        <tr>
            <td>2GT 6mm belt</td>
            <td>~5m</td>
            <td>XY Gantry (2x 1770mm for X, xxxmm for Y)</td>
            <td></td>
            <td><a href="https://www.Aliexpress.com/item/32952396111.html" rel="nofollow">Aliexpress</a></td>
        </tr>
        <tr>
            <td>2GT 9mm belt</td>
            <td>~3m</td>
            <td>Belted Z</td>
            <td></td>
            <td><a href="https://www.Aliexpress.com/item/32952396111.html" rel="nofollow">Aliexpress</a></td>
        </tr>
        <tr>
            <td>MR115ZZ</td>
            <td>14</td>
            <td></td>
            <td></td>
            <td><a href="https://www.Aliexpress.com/item/32499551293.html" rel="nofollow">Aliexpress</a></td>
        </tr>
        <tr>
            <td>6mm x 16mm length shaft/dowel pin</td>
            <td>6</td>
            <td>Cut linear shafts, dowel pins or some good m3 spacers(outer dia 6mm) will also work.</td>
            <td><a href="https://s.click.aliexpress.com/e/_99m43S" rel="nofollow">Aliexpress</a></td>
            <td><a href="https://www.aliexpress.com/item/1005003326358562.html" rel="nofollow">Aliexpress</a></td>
        </tr>
        <tr>
            <td>Hook spring 0.5x4x20mm</td>
            <td>6</td>
            <td>Bed coupling</td>
            <td></td>
            <td><a href="https://www.Aliexpress.com/item/1005001491389608.html" rel="nofollow">Aliexpress</a></td>
        </tr>
        <tr>
            <td>Diameter 5mm x 65mm length shaft or dowel pin</td>
            <td>3</td>
            <td>Bed Coupling</td>
            <td></td>
            <td><a href="https://www.Aliexpress.com/item/1005003150582428.html" rel="nofollow">Aliexpress</a></td>
        </tr>
        <tr>
            <td>10mm M4 threaded ball</td>
            <td>3</td>
            <td>Ride on M5 dowels to ensure bed coupling</td>
            <td></td>
            <td><a href="https://www.Aliexpress.com/item/4001141631405.html" rel="nofollow">Aliexpress</a></td>
        </tr>
    </tbody>
</table>
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

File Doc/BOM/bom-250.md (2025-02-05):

# BOM

<code>Status : work in progress</code>  
<code>Last updated : 2022-02-17</code>

<code> Fell free to [contact me](https://discord.gg/WZVP2HuAag) if you spot mistake or have question.</code>

## Read this first

## Table of contents

- [Kit](#0Kit)
- [Frame](#1Frame)
- [Fasteners](#2Fasteners)
- [Motion](#3Motion)
- [Electronics](#4Electronics)
- [Panels](#5Panels)
- [Other](#6Other)
- [Alternative bed coupling options](#7Alternative-bed-coupling-options)
- [Z counter weight](#8Z-counter-weight)

# 0.Kit

Some parts listed on the BOM can be purchased in kit format from below vendors

- [kb-3d.com store](https://kb-3d.com/store/81-snakeoilxy)

# 1.Frame

- [Main Frame](#main-frame)
- [Bed](#bed)
- [Gantry](#gantry)

## Main Frame

<table>
    <thead>
        <tr>
            <th>Item</th>
            <th>Quantity</th>
            <th>Misumi code</th>
        </tr>
    </thead>
	  <tbody>
        <tr>
            <td>3030 Extrusion 330mm</td>
            <td>3</td>
            <td>HFS6-3030-330</td>
        </tr>
        <tr>
            <td>3030 Extrusion 550mm</td>
            <td>4</td>
            <td>HFS6-3030-550</td>
        </tr>
        <tr>
            <td>3030 Extrusion 380mm</td>
            <td>5</td>
            <td>HFS6-3030-380</td>
        </tr>
        <tr>
            <td>3030 Extrusion 360mm</td>
            <td>6</td>
            <td>HFS6-3030-360</td>
        </tr>
        <tr>
            <td>3030, 30mm long, 20mm thick corner bracket<br>
            <a href="./corner-brackets.md" rel="nofollow">Check this if you don't have access to misumi brackets</a></td>
            <td>29</td>
            <td>HBLFSN6</td>
        </tr>
    </tbody>
</table>

<code>3030 extrusions are 8mm slot type, 2020 extrusions are 6mm slot type, 1515 extrusions are 3.4mm slot type
</code>

## Bed

### 1515 profile (recommended)

Instead of 1515 profile you can use [MakerBeamXL](https://www.makerbeam.com/makerbeamxl/), you just need to print a different version of the mountings.

<table>
    <thead>
        <tr>
            <th>Item</th>
            <th>Quantity</th>
            <th>Misumi code</th>
        </tr>
    </thead>
	  <tbody>
        <tr>
            <td>1515 Extrusion 260mm</td>
            <td>2</td>
            <td>HFS3-1515-260</td>
        </tr>
        <tr>
            <td>1515 Extrusion 235mm</td>
            <td>2</td>
            <td>HFS3-1515-235</td>
        </tr>
        <tr>
            <td>1515 Corner bracket</td>
            <td>4</td>
            <td>HBLTBS3</td>
        </tr>
    </tbody>
</table>

### 2020 profile

<table>
    <thead>
        <tr>
            <th>Item</th>
            <th>Quantity</th>
            <th>Misumi code</th>
        </tr>
    </thead>
	  <tbody>
        <tr>
            <td>2020 Extrusion 240mm</td>
            <td>2</td>
            <td>HFS5-2020-240</td>
        </tr>
        <tr>
            <td>2020 Extrusion 220mm</td>
            <td>2</td>
            <td>HFS5-2020-220</td>
        </tr>
        <tr>
            <td>2020 Corner bracket</td>
            <td>4</td>
            <td>HBLSS5</td>
        </tr>
    </tbody>
</table>

## Gantry

### 1515 profile (recommended)

Instead of 1515 profile you can use [MakerBeamXL](https://www.makerbeam.com/makerbeamxl/), you just need to print a different version of the mountings.

<table>
    <thead>
        <tr>
            <th>Item</th>
            <th>Quantity</th>
            <th>Misumi code</th>
        </tr>
    </thead>
	  <tbody>
        <tr>
            <td>1515 Extrusion 360mm</td>
            <td>1</td>
            <td>HFS3-1515-360</td>
        </tr>
    </tbody>
</table>

### 2020 profile

<table>
    <thead>
        <tr>
            <th>Item</th>
            <th>Quantity</th>
            <th>Misumi code</th>
        </tr>
    </thead>
	  <tbody>
        <tr>
            <td>2020 Extrusion 360mm</td>
            <td>1</td>
            <td>HFS5-2020-360</td>
        </tr>
    </tbody>
</table>

# 2.Fasteners

## Nuts and bolt

<table>
    <thead>
        <tr>
            <th>Item</th>
            <th>Quantity</th>
            <th>Description</th>
            <th>default link/affiliate link</th>
            <th>non-affiliate link</th>
        </tr>
    </thead>
    <tbody>
        <tr>
            <td>2020 M3 T-nut</td>
            <td>20</td>
            <td>for 2020 bed frame and gantry</td>
            <td><a href="https://s.click.aliexpress.com/e/_ASabWc" rel="nofollow">Aliexpress</a></td>
            <td><a href="https://www.aliexpress.com/item/4000293743251.html" rel="nofollow">Aliexpress</a></td>
        </tr>
        <tr>
            <td>2020 M5 T-nut</td>
            <td>15</td>
            <td> for 2020 bed frame and gantry</td>
            <td><a href="https://s.click.aliexpress.com/e/_ASabWc" rel="nofollow">Aliexpress</a></td>
            <td><a href="https://www.aliexpress.com/item/4000293743251.html" rel="nofollow">Aliexpress</a></td>
        </tr>
        <tr>
            <td>Square nut M3(hex nut also works)</td>
            <td>30</td>
            <td> for 1515 bed frame and gantry</td>
            <td></td>
            <td></td>
        </tr>
        <tr>
            <td>3030 M3 T-nut</td>
            <td>60</td>
            <td></td>
            <td><a href="https://s.click.aliexpress.com/e/_ASabWc" rel="nofollow">Aliexpress</a></td>
            <td><a href="https://www.aliexpress.com/item/4000293743251.html" rel="nofollow">Aliexpress</a></td>
        </tr>
        <tr>
            <td>3030 M5 T-nut</td>
            <td>10</td>
            <td></td>
            <td><a href="https://s.click.aliexpress.com/e/_ASabWc" rel="nofollow">Aliexpress</a></td>
            <td><a href="https://www.aliexpress.com/item/4000293743251.html" rel="nofollow">Aliexpress</a></td>
        </tr>
        <tr>
            <td>3030 M6 T-nut</td>
            <td>160</td>
            <td></td>
            <td><a href="https://s.click.aliexpress.com/e/_ASabWc" rel="nofollow">Aliexpress</a></td>
            <td><a href="https://www.aliexpress.com/item/4000293743251.html" rel="nofollow">Aliexpress</a></td>
        </tr>
    </tbody>
</table>

<table>
    <thead>
        <tr>
            <th>Item</th>
            <th>Quantity</th>
            <th>Description</th>
            <th>default link/affiliate link</th>
            <th>non-affiliate link</th>
        </tr>
    </thead>
    <tbody>
        <tr>
            <td>M3x3-HeatSet</td>
            <td>50</td>
            <td>M3 X D4.2 X L3.0</td>
            <td><a href="https://s.click.aliexpress.com/e/_Ad1n92" rel="nofollow">Aliexpress</a></td>
            <td><a href="https://www.Aliexpress.com/item/1005002526998853.html" rel="nofollow">Aliexpress</a></td>
        </tr>
        <tr>
            <td>M3x4-HeatSet</td>
            <td>150</td>
            <td>M3 X D4.2 X L4.0</td>
            <td><a href="https://s.click.aliexpress.com/e/_Ad1n92" rel="nofollow">Aliexpress</a></td>
            <td><a href="https://www.Aliexpress.com/item/1005002526998853.html" rel="nofollow">Aliexpress</a></td>
        </tr>
        <tr>
            <td>M3x5x4-HeatSet</td>
            <td>5</td>
            <td>M3 X D5.0 X L4.0 (for sherpa mini)</td>
            <td><a href="https://s.click.aliexpress.com/e/_AcLT3I" rel="nofollow">Aliexpress</a></td>
            <td><a href="https://www.aliexpress.com/item/4000232858343.html" rel="nofollow">Aliexpress</a></td>
        </tr>
        <tr>
            <td>M4-HeatSet</td>
            <td>3</td>
            <td>M4 X D6.0 X L4.0 (for threaded ball bed coupler)</td>
            <td><a href="https://s.click.aliexpress.com/e/_A9WsSs" rel="nofollow">Aliexpress</a></td>
            <td><a href="https://www.Aliexpress.com/item/4000232925592.html" rel="nofollow">Aliexpress</a></td>
        </tr>
        <tr>
            <td>M5-HeatSet</td>
            <td>10</td>
            <td>M5 X D7.0 X L7.0</td>
            <td><a href="https://s.click.aliexpress.com/e/_AZBpZE" rel="nofollow">Aliexpress</a></td>
            <td><a href="https://www.aliexpress.com/item/4000232990523.html" rel="nofollow">Aliexpress</a></td>
        </tr>
    </tbody>
</table>

<table>
    <thead>
        <tr>
            <td>Item</td>
            <td>Quantity</td>
            <td>Description</td>
            <td>Norm</td>
        </tr>
    </thead>
    <tbody>
        <tr>
            <td>Button head M3x6</td>
            <td>75</td>
            <td></td>
            <td>ISO 7380 / DIN 7380</td>
        </tr>
        <tr>
            <td>Button head M3x8</td>
            <td>3</td>
            <td></td>
            <td>ISO 7380 / DIN 7380</td>
        </tr>
        <tr>
            <td>Button head M3x10</td>
            <td>14</td>
            <td></td>
            <td>ISO 7380 / DIN 7380</td>
        </tr>
        <tr>
            <td>Button head M3x12</td>
            <td>10</td>
            <td></td>
            <td>ISO 7380 / DIN 7380</td>
        </tr>
        <tr>
            <td>Button head M3x16</td>
            <td>5</td>
            <td></td>
            <td>ISO 7380 / DIN 7380</td>
        </tr>
        <tr>
            <td>Button head M3x20</td>
            <td>1</td>
            <td></td>
            <td>ISO 7380 / DIN 7380</td>
        </tr>
        <tr>
            <td>Button head M3x30</td>
            <td>4</td>
            <td></td>
            <td>ISO 7380 / DIN 7380</td>
        </tr>
        <tr>
            <td>Button head M3x35</td>
            <td>2</td>
            <td></td>
            <td>ISO 7380 / DIN 7380</td>
        </tr>
        <tr>
            <td>Button head M4x6</td>
            <td>4</td>
            <td></td>
            <td>ISO 7380 / DIN 7380</td>
        </tr>
        <tr>
            <td>Button head M4x25</td>
            <td>2</td>
            <td></td>
            <td>ISO 7380 / DIN 7380</td>
        </tr>
        <tr>
            <td>Button head M5x10</td>
            <td>6</td>
            <td></td>
            <td>ISO 7380 / DIN 7380</td>
        </tr>
        <tr>
            <td>Button head M5x25</td>
            <td>3</td>
            <td></td>
            <td>ISO 7380 / DIN 7380</td>
        </tr>
        <tr>
            <td>Button head M5x40</td>
            <td>5</td>
            <td></td>
            <td>ISO 7380 / DIN 7380</td>
        </tr>
        <tr>
            <td>Button head M5x45</td>
            <td>1</td>
            <td></td>
            <td>ISO 7380 / DIN 7380</td>
        </tr>
        <tr>
            <td>Button head M5x50</td>
            <td>8</td>
            <td></td>
            <td>ISO 7380 / DIN 7380</td>
        </tr>
        <tr>
            <td>Button head M6x10</td>
            <td>17</td>
            <td></td>
            <td>ISO 7380 / DIN 7380</td>
        </tr>
        <tr>
            <td>Button head M6x12</td>
            <td>10</td>
            <td></td>
            <td>ISO 7380 / DIN 7380</td>
        </tr>
        <tr>
            <td>Button head M6x14</td>
            <td>17</td>
            <td></td>
            <td>ISO 7380 / DIN 7380</td>
        </tr>
        <tr>
            <td>Button head M6x16</td>
            <td>48</td>
            <td></td>
            <td>ISO 7380 / DIN 7380</td>
        </tr>
        <tr>
            <td>Button head M6x20</td>
            <td>4</td>
            <td></td>
            <td>ISO 7380 / DIN 7380</td>
        </tr>
        <tr>
            <td>Button head M6x25</td>
            <td>1</td>
            <td></td>
            <td>ISO 7380 / DIN 7380</td>
        </tr>
        <tr>
            <td>Button head M6x35</td>
            <td>6</td>
            <td></td>
            <td>ISO 7380 / DIN 7380</td>
        </tr>
        <tr>
            <td>Button head M8x12</td>
            <td>4</td>
            <td></td>
            <td>ISO 7380 / DIN 7380</td>
        </tr>
        <tr>
            <td>Button head M8x20</td>
            <td>30</td>
			<td>Only needed 8 if you buy HCJ_Joint.</br> The other 22 M8x20 bolts will be included in HCJ joint set</td>
            <td>ISO 7380 / DIN 7380</td>
        </tr>
    </tbody>
</table>

<table>
    <thead>
        <tr>
            <td>Item</td>
            <td>Quantity</td>
            <td>Description</td>
            <td>Norm</td>
        </tr>
    </thead>
    <tbody>
        <tr>
            <td>Socket head M2.5x12</td>
            <td>2</td>
            <td></td>
            <td>DIN 912 / ISO 4762</td>
        </tr>
        <tr>
            <td>Socket head M3x6</td>
            <td>6</td>
            <td></td>
            <td>DIN 912 / ISO 4762</td>
        </tr>
        <tr>
            <td>Socket head M3x8</td>
            <td>57</td>
            <td></td>
            <td>DIN 912 / ISO 4762</td>
        </tr>
        <tr>
            <td>Socket head M3x10</td>
            <td>107</td>
            <td></td>
            <td>DIN 912 / ISO 4762</td>
        </tr>
        <tr>
            <td>Socket head M3x12</td>
            <td>18</td>
            <td></td>
            <td>DIN 912 / ISO 4762</td>
        </tr>
        <tr>
            <td>Socket head M3x14</td>
            <td>18</td>
            <td></td>
            <td>DIN 912 / ISO 4762</td>
        </tr>
        <tr>
            <td>Socket head M3x16</td>
            <td>10</td>
            <td></td>
            <td>DIN 912 / ISO 4762</td>
        </tr>
        <tr>
            <td>Socket head M3x20</td>
            <td>3</td>
            <td></td>
            <td>DIN 912 / ISO 4762</td>
        </tr>
        <tr>
            <td>Socket head M3x25</td>
            <td>8</td>
            <td></td>
            <td>DIN 912 / ISO 4762</td>
        </tr>
        <tr>
            <td>Socket head M3x35</td>
            <td>9</td>
            <td></td>
            <td>DIN 912 / ISO 4762</td>
        </tr>
        <tr>
            <td>Socket head M3x40</td>
            <td>15</td>
            <td></td>
            <td>DIN 912 / ISO 4762</td>
        </tr>
        <tr>
            <td>Socket head M3x45</td>
            <td>3</td>
            <td></td>
            <td>DIN 912 / ISO 4762</td>
        </tr>
        <tr>
            <td>Socket head M3x70</td>
            <td>6</td>
            <td></td>
            <td>DIN 912 / ISO 4762</td>
        </tr>
        <tr>
            <td>Socket head M6x14</td>
            <td>56</td>
            <td></td>
            <td>DIN 912 / ISO 4762</td>
        </tr>
    </tbody>
</table>

<table>
    <thead>
        <tr>
            <td>Item</td>
            <td>Quantity</td>
            <td>Description</td>
            <td>Norm</td>
        </tr>
    </thead>
    <tbody>
        <tr>
            <td>Grub M3x8</td>
            <td>5</td>
            <td></td>
            <td>DIN 913 / ISO 4026</td>
        </tr>
        <tr>
            <td>Grub M4x12</td>
            <td>3</td>
            <td>(for threaded ball bed coupler)</td>
            <td>DIN 913 / ISO 4026</td>
        </tr>
        <tr>
            <td>Self taping screw M2x10</td>
            <td>4</td>
            <td></td>
            <td>-</td>
        </tr>
    </tbody>
</table>

<table>
    <thead>
        <tr>
            <td>Item</td>
            <td>Quantity</td>
            <td>Description</td>
            <td>Norm</td>
        </tr>
    </thead>
    <tbody>
        <tr>
            <td>Hex M3 nut</td>
            <td>8</td>
            <td></td>
            <td>DIN 934 / ISO 4032</td>
        </tr>
        <tr>
            <td>Hex M4 nut</td>
            <td>2</td>
            <td></td>
            <td>DIN 934 / ISO 4032</td>
        </tr>
        <tr>
            <td>Hex M5 nut</td>
            <td>4</td>
            <td></td>
            <td>DIN 934 / ISO 4032</td>
        </tr>
    </tbody>
</table>

<table>
    <thead>
        <tr>
            <td>Item</td>
            <td>Quantity</td>
            <td>Description</td>
            <td>Norm</td>
        </tr>
    </thead>
    <tbody>
        <tr>
            <td>Small M3 washer</td>
            <td>71</td>
            <td></td>
            <td>ISO 7092 / DIN 433</td>
        </tr>
        <tr>
            <td>Small M5 washer</td>
            <td>2</td>
            <td></td>
            <td>ISO 7092 / DIN 433</td>
        </tr>
        <tr>
            <td>Normal M5 washer</td>
            <td>4*</td>
            <td>Check out a few lines below </td>
            <td>DIN 125 / ISO 7089</td>
        </tr>
        <tr>
            <td>Normal M6 washer</td>
            <td>91*</td>
            <td>Check out a few lines below </td>
            <td>DIN 125 / ISO 7089</td>
        </tr>
        <tr>
            <td>Wide M3 washer</td>
            <td>16</td>
            <td></td>
            <td>DIN 9021 / ISO 7093</td>
        </tr>
        <tr>
            <td>Spring M3 washer </td>
            <td>60</td>
            <td></td>
            <td>DIN 127 </td>
        </tr>
        <tr>
            <td>Normal M3 washer</td>
            <td>370</td>
            <td>We don't have a simple way to calculate the amount of washers you will need, if your budget can afford it buy as many as bolts </td>
            <td>DIN 125 / ISO 7089</td>
        </tr>
        <tr>
            <td>Normal M4 washer</td>
            <td>6</td>
            <td>We don't have a simple way to calculate the amount of washers you will need, if your budget can afford it buy as many as bolts </td>
            <td>DIN 125 / ISO 7089</td>
        </tr>
        <tr>
            <td>Normal M5 washer</td>
            <td>23</td>
            <td>We don't have a simple way to calculate the amount of washers you will need, if your budget can afford it buy as many as bolts </td>
            <td>DIN 125 / ISO 7089</td>
        </tr>
        <tr>
            <td>Normal M6 washer</td>
            <td>159</td>
            <td>We don't have a simple way to calculate the amount of washers you will need, if your budget can afford it buy as many as bolts </td>
            <td>DIN 125 / ISO 7089</td>
        </tr>
    </tbody>
</table>

# 3.Motion

<table>
    <thead>
        <tr>
            <th>Item</th>
            <th>Quantity</th>
            <th>Description</th>
            <th>default link/affiliate link</th>
            <th>non-affiliate link</th>
        </tr>
    </thead>
    <tbody>
        <tr>
            <td>MGN12H 300mm</td>
            <td>5</td>
            <td></td>
            <td></td>
            <td><a href="https://www.aliexpress.com/item/32829826159.html" rel="nofollow">Aliexpress</a></td>
        </tr>
        <tr>
            <td>MGN12H 320mm</td>
            <td>1</td>
            <td></td>
            <td></td>
            <td><a href="https://www.aliexpress.com/item/32829826159.html" rel="nofollow">Aliexpress</a></td>
        </tr>
        <tr>
            <td>20T 6mm Pulley (5mm bore)</td>
            <td>2</td>
            <td></td>
            <td></td>
            <td><a href="https://www.Aliexpress.com/item/33023279793.html" rel="nofollow">Aliexpress</a></td>
        </tr>
        <tr>
            <td>16T 6mm Pulley (5mm bore)</td>
            <td>3</td>
            <td></td>
            <td></td>
            <td><a href="https://www.Aliexpress.com/item/33002989677.html" rel="nofollow">Aliexpress</a></td>
        </tr>
        <tr>
            <td>80T 6mm Pulley (5mm bore)</td>
            <td>3</td>
            <td></td>
            <td></td>
            <td><a href="https://www.Aliexpress.com/item/1005001700640216.html" rel="nofollow">Aliexpress</a></td>
        </tr>
        <tr>
            <td>20T 9mm Pulley (5mm bore)</td>
            <td>3</td>
            <td></td>
            <td></td>
            <td><a href="https://www.Aliexpress.com/item/33023279793.html" rel="nofollow">Aliexpress</a></td>
        </tr>
        <tr>
            <td>20T 6mm Smooth Idler (5mm bore)</td>
            <td>10</td>
            <td></td>
            <td></td>
            <td><a href="https://www.Aliexpress.com/item/33023133633.html" rel="nofollow">Aliexpress</a></td>
        </tr>
        <tr>
            <td>20T 6mm Tooth Idler (5mm bore)</td>
            <td>2</td>
            <td></td>
            <td></td>
            <td><a href="https://www.Aliexpress.com/item/33023133633.html" rel="nofollow">Aliexpress</a></td>
        </tr>
        <tr>
            <td>20T 9mm Tooth idler (5mm bore)</td>
            <td>3</td>
            <td></td>
            <td></td>
            <td><a href="https://www.Aliexpress.com/item/33023133633.html" rel="nofollow">Aliexpress</a></td>
        </tr>
        <tr>
            <td>Close loop 188-2GT-6 RF belt</td>
            <td>3</td>
            <td></td>
            <td></td>
            <td><a href="https://www.Aliexpress.com/item/4000397043382.html" rel="nofollow">Aliexpress</a></td>
        </tr>
        <tr>
            <td>2GT 6mm belt</td>
            <td>~4m</td>
            <td>XY Gantry</td>
            <td></td>
            <td><a href="https://www.Aliexpress.com/item/32952396111.html" rel="nofollow">Aliexpress</a></td>
        </tr>
        <tr>
            <td>2GT 9mm belt</td>
            <td>~3m</td>
            <td>Belted Z</td>
            <td></td>
            <td><a href="https://www.Aliexpress.com/item/32952396111.html" rel="nofollow">Aliexpress</a></td>
        </tr>
        <tr>
            <td>MR115ZZ</td>
            <td>14</td>
            <td></td>
            <td></td>
            <td><a href="https://www.Aliexpress.com/item/32499551293.html" rel="nofollow">Aliexpress</a></td>
        </tr>
        <tr>
            <td>6mm x 16mm length shaft/dowel pin</td>
            <td>6</td>
            <td>Cut linear shafts, dowel pins or some good m3 spacers(outer dia 6mm) will also work.</td>
            <td><a href="https://s.click.aliexpress.com/e/_99m43S" rel="nofollow">Aliexpress</a></td>
            <td><a href="https://www.aliexpress.com/item/1005003326358562.html" rel="nofollow">Aliexpress</a></td>
        </tr>
        <tr>
            <td>Hook spring 0.5x4x20mm</td>
            <td>6</td>
            <td>Bed coupling</td>
            <td></td>
            <td><a href="https://www.Aliexpress.com/item/1005001491389608.html" rel="nofollow">Aliexpress</a></td>
        </tr>
        <tr>
            <td>Diameter 5mm x 65mm length shaft or dowel pin</td>
            <td>3</td>
            <td>Bed Coupling</td>
            <td></td>
            <td><a href="https://www.Aliexpress.com/item/1005003150582428.html" rel="nofollow">Aliexpress</a></td>
        </tr>
        <tr>
            <td>10mm M4 threaded ball</td>
            <td>3</td>
            <td>Ride on M5 dowels to ensure bed coupling</td>
            <td></td>
            <td><a href="https://www.Aliexpress.com/item/4001141631405.html" rel="nofollow">Aliexpress</a></td>
        </tr>
    </tbody>
</table>
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

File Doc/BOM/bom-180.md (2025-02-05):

# BOM

<code>Status : work in progress</code>  
<code>Last updated : 2022-02-17</code>

<code> Fell free to [contact me](https://discord.gg/WZVP2HuAag) if you spot mistake or have question.</code>

## Read this first

## Table of contents

- [Kit](#0Kit)
- [Frame](#1Frame)
- [Fasteners](#2Fasteners)
- [Motion](#3Motion)
- [Electronics](#4Electronics)
- [Panels](#5Panels)
- [Other](#6Other)
- [Alternative bed coupling options](#7Alternative-bed-coupling-options)
- [Z counter weight](#8Z-counter-weight)

# 0.Kit

Some parts listed on the BOM can be purchased in kit format from below vendors

- [kb-3d.com store](https://kb-3d.com/store/81-snakeoilxy)

# 1.Frame

- [Main Frame](#main-frame)
- [Bed](#bed)
- [Gantry](#gantry)

## Main Frame

<table>
    <thead>
        <tr>
            <th>Item</th>
            <th>Quantity</th>
            <th>Misumi code</th>
        </tr>
    </thead>
	  <tbody>
        <tr>
            <td>3030 Extrusion 280mm</td>
            <td>3</td>
            <td>HFS6-3030-280</td>
        </tr>
        <tr>
            <td>3030 Extrusion 500mm</td>
            <td>4</td>
            <td>HFS6-3030-500</td>
        </tr>
        <tr>
            <td>3030 Extrusion 310mm</td>
            <td>11</td>
            <td>HFS6-3030-310</td>
        </tr>
        <tr>
            <td>3030, 30mm long, 20mm thick corner bracket<br>
            <a href="./corner-brackets.md" rel="nofollow">Check this if you don't have access to misumi brackets</a></td>
            <td>29</td>
            <td>HBLFSN6</td>
        </tr>
    </tbody>
</table>

<code>3030 extrusions are 8mm slot type, 2020 extrusions are 6mm slot type, 1515 extrusions are 3.4mm slot type
</code>

## Bed
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

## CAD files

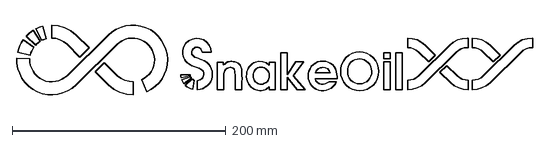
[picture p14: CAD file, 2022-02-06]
Doc/logo/SnakeOilXY_Full_Logo2.dxf
483.8 x 70.5 mm

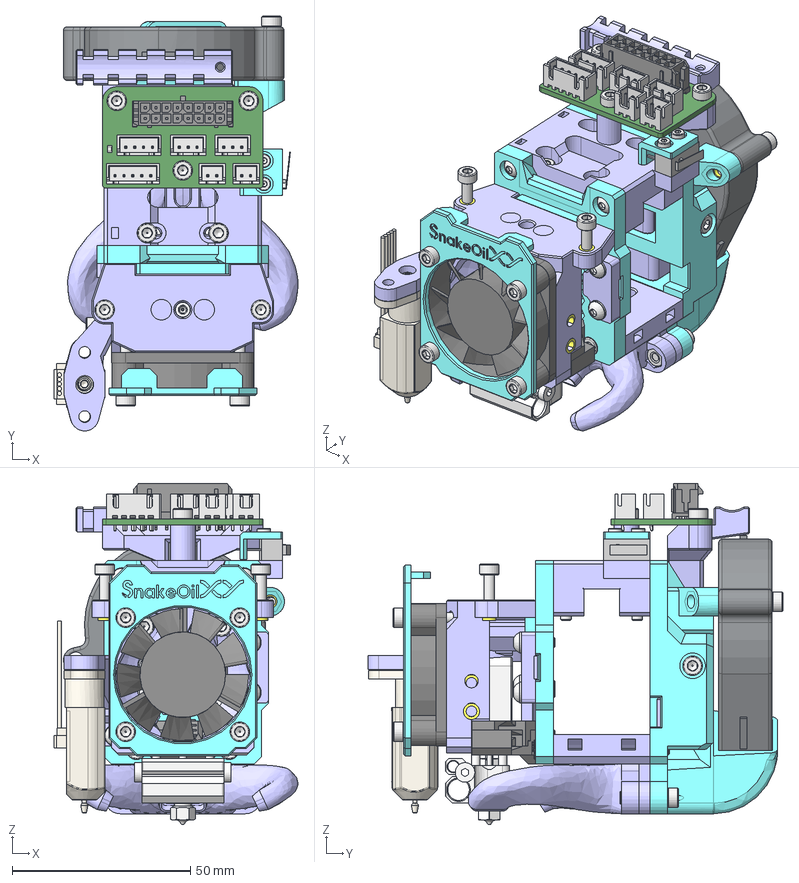
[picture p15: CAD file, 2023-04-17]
WIP/component-assembly/toolhead-sherpa-pcb-1515-assembly.FCStd
68.4 x 116.3 x 95.6 mm
mosquito-hotend
mosquito_support
5015 fan
4010-fan
BL-touch v3.x002
M3x10-Screw189
M3-Nut027
M3-Nut030
M3-Nut009
M3x40-Screw001
M3x40-Screw
M3-Nut026
M3x35-Screw003
M3x35-Screw004
M3x20-Screw
M3x12-Screw
M3x10-Screw186
M3x10-Screw
M3x12-Screw066
M3x10-Screw187
M3x10-Screw188
M3x10-Screw199
M2.5x12-Screw
M2.5x12-Screw001
M3x25-Screw030
M3x25-Screw
M3x20-Screw024
M3x25-Screw029
M3x25-Screw004
M3x20-Screw023
M3x35-Screw
M3x35-Screw005
dragon_support
face-plate
dragon-mount-mod
mosquito-mount-mod
extruder-belt-tesioner
extruder-belt-tesioner001
endstop-switch
endstop-cap
M2x10-Screw
M2x10-Screw001
M3x4-HeatSet
M3x4-HeatSet001
M3x4-HeatSet003
M3x4-HeatSet004
M3x4-HeatSet009
M3x4-HeatSet010
M3x4-HeatSet012
M3x4-HeatSet013
M3x4-HeatSet017
M3x4-HeatSet018
duct-tri-horn
M3-Nut032
M3-Nut033
M3x12-Screw074
M3x12-Screw075
M3-HeatSet
M3x4-HeatSet019
bltouch-mount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

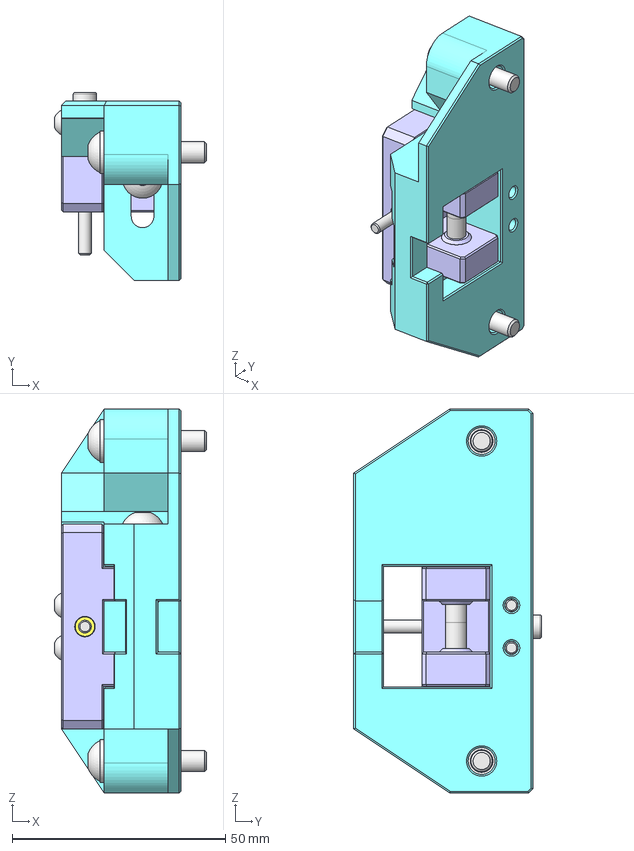
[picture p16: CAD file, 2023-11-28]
2023-Nov-28th-patch/new-front-idler/front-idler-assembly.step
35.6 x 44.0 x 90.0 mm
idler-housing001
idler-mounter-rev (Mirror #2)001
M5x45-Screw
M3x25-Screw x 2
M3-Insert
M3x35-Screw
M5-Washer x 2
M5x25-Screw x 2

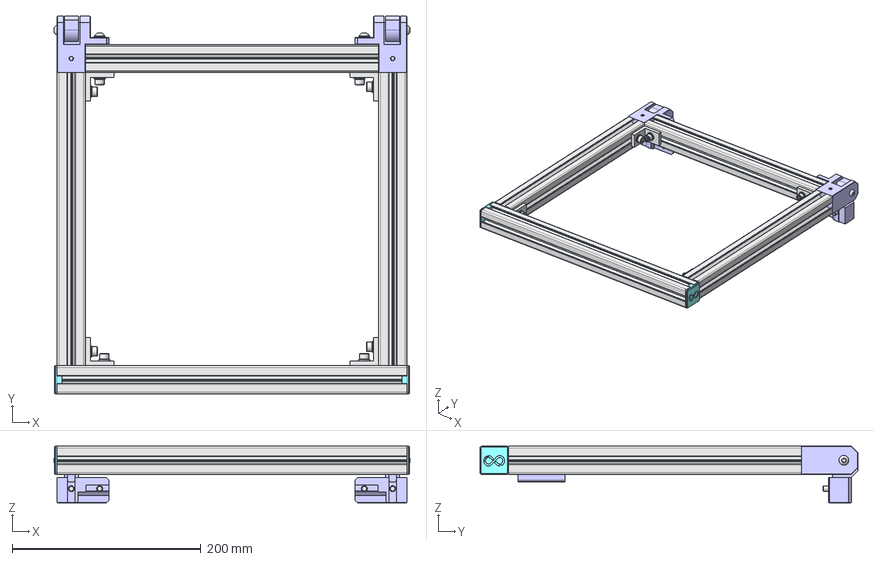
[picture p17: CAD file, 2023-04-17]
WIP/component-assembly/top-lid-assembly.FCStd
376.6 x 400.0 x 60.0 mm
3030-370mm-top-lid-001
3030-310mm-top-lid-001
3030-310mm-top-lid-002
3030-310mm-top-lid-003
M6-Washer005
M6x12-Screw113
M6x20-Screw001
lid-left-bottom-hinge
M8x30-Screw001
M6-Washer001
M6x14-Screw
M6-Nut
M6x10-Screw120
lid-left-top-hinge
M8x30-Screw
M6-Washer156
M6x14-Screw001
M6-Nut001
M6x10-Screw001
lid-right-top-hinge
M6-Washer004
M6x12-Screw112
M6x20-Screw
lid-right-bottom-hinge
M6-Washer011
M6-Washer010
M6x14-Screw009
M6x14-Screw010
L-corner-bracket028
M6x14-Screw011
M6-Washer012
M6-Washer013
M6x14-Screw012
L-corner-bracket029
M6-Washer006
M6-Washer157
M6x14-Screw013
M6x14-Screw014
L-corner-bracket030
M6-Washer159
M6-Washer158
M6x14-Screw015
M6x14-Screw016
L-corner-bracket010
lid-end-cap001
lid-end-cap002

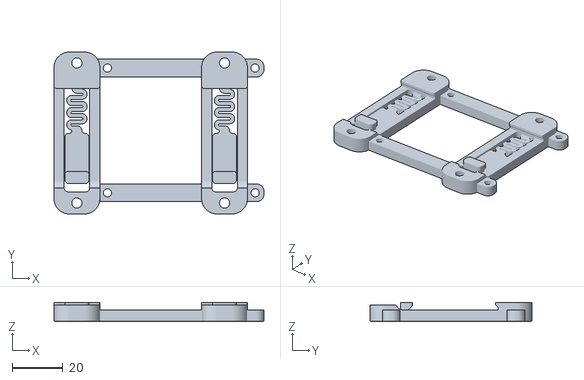
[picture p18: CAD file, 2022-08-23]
BETA3_Standard_Release_STL/STLs/Panels/Back-panel/Bottom/OPTIONAL_1x_raspberry-full-size-din-mounter.stl
82.5 x 63.6 x 7.60

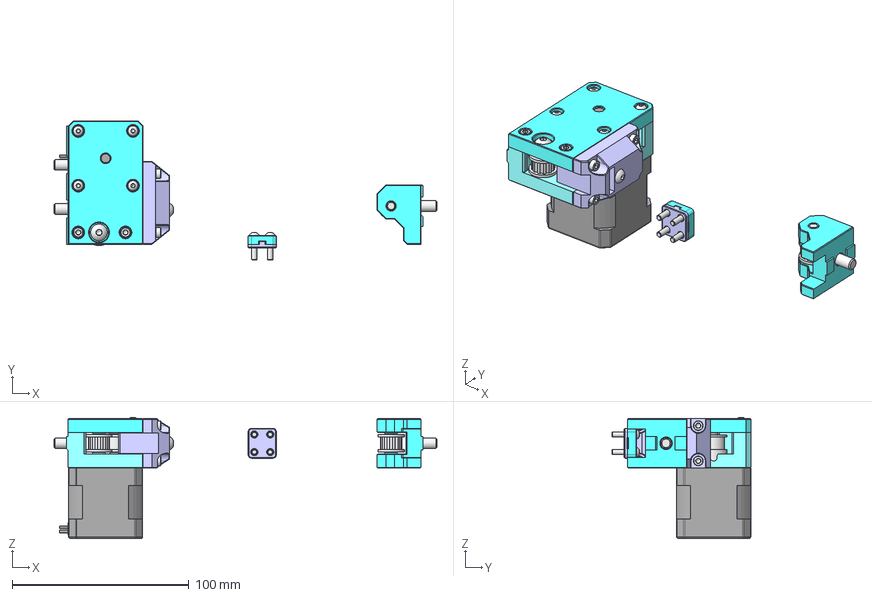
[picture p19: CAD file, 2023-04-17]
WIP/component-assembly/4PR-assembly.FCStd
217.0 x 79.0 x 68.7 mm
motor
20t-pulley-6mm
MR115ZZ
smooth-idler-6mm
tooth-idler-6mm
c-motor-mount-inner-plate
c-idler-housing
c-tesioner-cap-nut
M3-HeatSet
M3-HeatSet001
M3-HeatSet002
M3-HeatSet003
M3-HeatSet004
M3-HeatSet005
M3x25-Screw
M3x25-Screw001
M3x30-Screw
M3x30-Screw007
M3x30-Screw008
M3x30-Screw009
M6x14-Screw001
M6x14-Screw002
M5x25-Screw001
M3x10-Screw
M3x10-Screw004
M3x10-Screw005
M3x10-Screw006
M4x20-Screw
M4-HeatSet
M5x20-ThreadedRod
M4-Nut
c-motor-mount-outer-plate
c-motor-shaft-spacer
c-belt-mounter-top
c-belt-mounter-bottom
M3x14-Screw
M3x14-Screw001
M3x14-Screw002
M3x14-Screw003
c-idler-mount
tooth-idler-6mm001
M5x25-Screw
M6x14-Screw

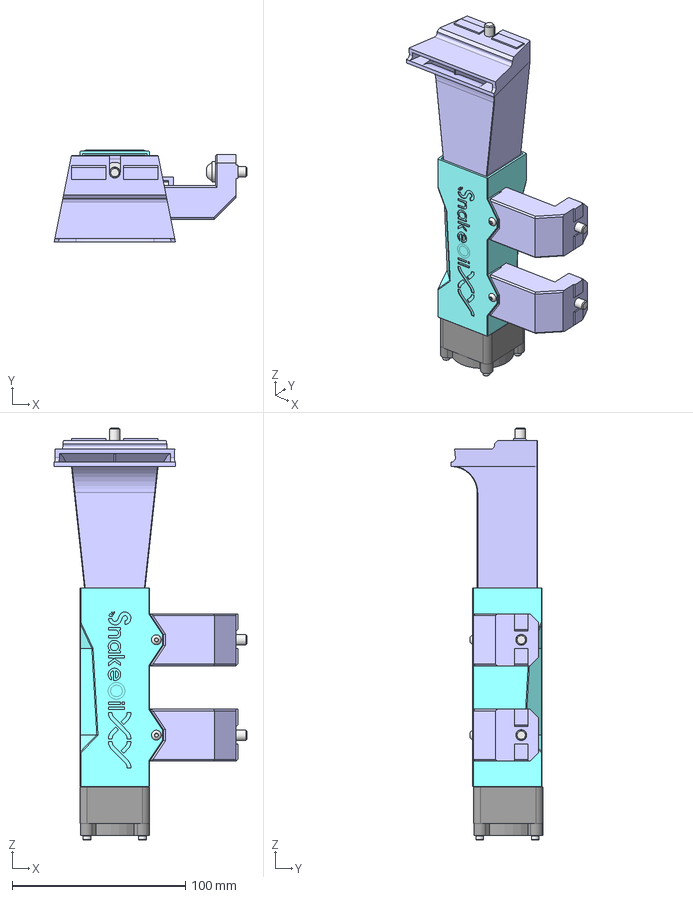
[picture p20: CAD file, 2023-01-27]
WIP/component-assembly/side-blower-4028-assembly.FCStd
111.2 x 53.0 x 237.7 mm
180-duct-angled
fan-mounter
mounter-arm
mounter-arm001
M3-HeatSet
M3-HeatSet001
M2.5-HeatSet
M2.5-HeatSet001
M2.5-HeatSet002
M2.5-HeatSet003
M6-Washer
M6-Washer001
M6x20-Screw
M6x20-Screw001
M6-Washer002
M6x16-Screw
M3x20-Screw
M3x20-Screw001
M2.5x30-Screw
M2.5x30-Screw001
M2.5x30-Screw002
M2.5x30-Screw003
4028-fan

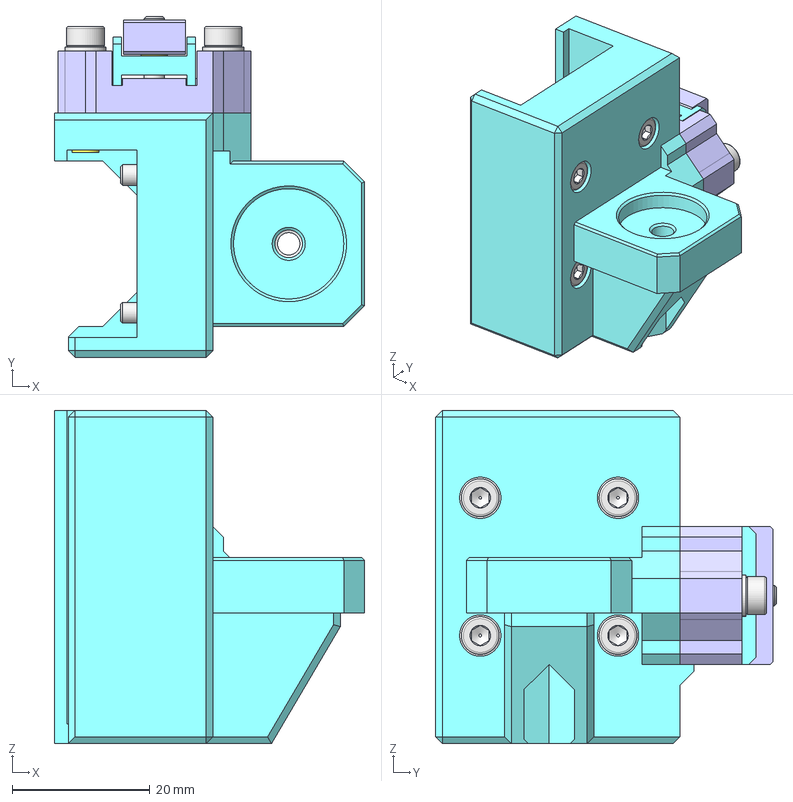
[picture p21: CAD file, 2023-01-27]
WIP/component-assembly/z-block-mount-left-assembly.FCStd
45.0 x 49.5 x 48.4 mm
z-belt-mounter-clamp-nut
z-belt-block-mount
z-belt-mounter-middle
M3-Washer
M3-Washer008
M3-Washer009
M3-Washer010
M3x10-Screw003
M3x10-Screw004
M3x10-Screw005
M3x10-Screw
M3x4-HeatSet
M3x4-HeatSet001
M3x4-HeatSet002
M3-Washer006
M3-Washer007
M3x14-Screw
M3x14-Screw001
M3x12-Screw
z-rail-block-mount-left
M3x25-Screw
M3x25-Screw001
M4-Nut

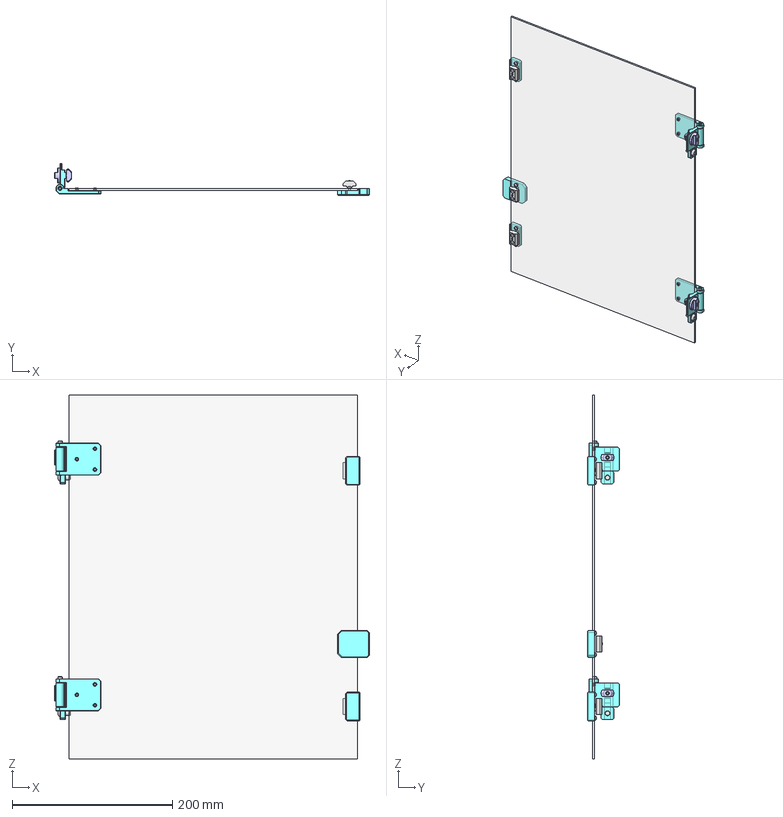
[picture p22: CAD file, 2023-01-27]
WIP/component-assembly/front-panel-assembly.FCStd
393.0 x 40.0 x 454.0 mm
frame-magnet-mount002
frame-magnet-mount
frame-magnet-mount001
door-magnet-mount-large
door-magnet-mount-small
door-magnet-mount-small001
M3-Washer022
M3-Washer
M3-Washer030
M3-Washer029
M3-Washer031
M3-Washer032
M3x6-Screw
M3x6-Screw026
M3x6-Screw035
M3x6-Screw036
M3x6-Screw034
M3x6-Screw033
M3x3-HeatSet003
M3x3-HeatSet004
M3x3-HeatSet005
M3x3-HeatSet006
M3x3-HeatSet007
M3x3-HeatSet008
6x3-magnet
6x3-magnet001
6x3-magnet002
6x3-magnet003
6x3-magnet004
6x3-magnet005
19x5x1p5m-magnet
19x5x1p5m-magnet001
19x5x1p5m-magnet002
M3x8-Screw044
M3x8-Screw
M3x8-Screw045
panel-360x454x3mm
side-hinge001
M3x16-Screw001
knob001
M6x12-Screw001
M3x6-Screw024
M3x6-Screw023
M3x6-Screw025
M3x40-Screw001
front-hinge001
nut
hinge-support
M3x4-HeatSet002
M3x4-HeatSet003
M3x4-HeatSet004
M3x4-HeatSet005
M3x4-HeatSet006
side-hinge
M3x16-Screw
knob
M6x12-Screw
M3x6-Screw004
M3x6-Screw003
M3x6-Screw022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

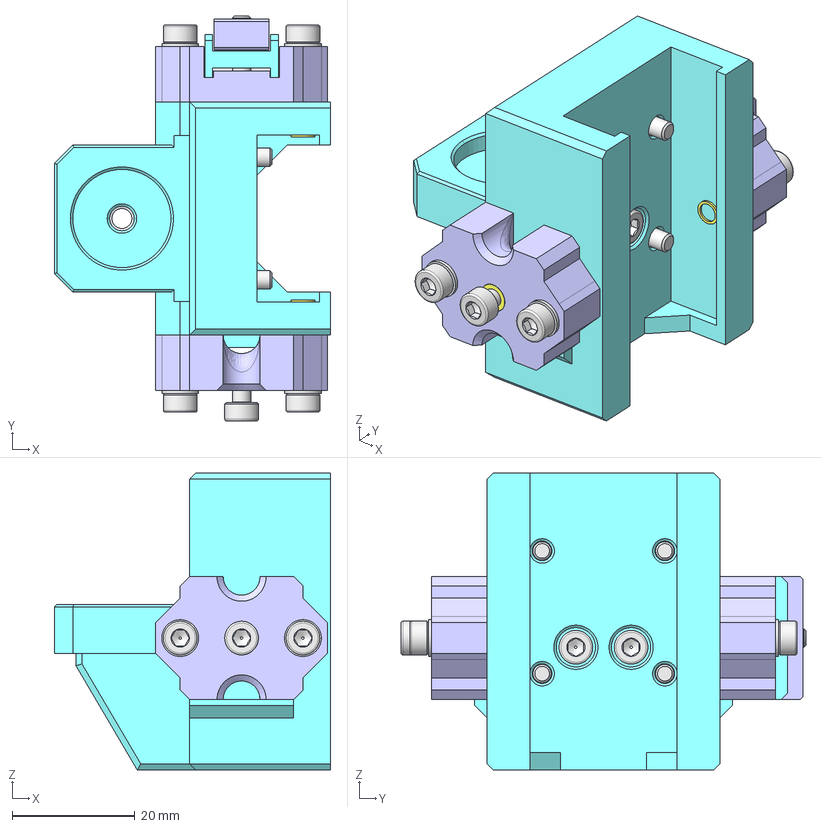
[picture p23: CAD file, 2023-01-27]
WIP/component-assembly/z-block-mount-right-counter-weight-assembly.FCStd
45.0 x 66.0 x 48.4 mm
z-belt-mounter-clamp-nut001
z-belt-mounter-middle001
z-belt-block-mount001
M3-Washer
M3-Washer020
M3-Washer021
M3-Washer022
M3x10-Screw
M3x10-Screw004
M3x10-Screw005
M3x10-Screw006
M3x4-HeatSet006
M3x4-HeatSet007
M3x4-HeatSet010
M3x12-Screw001
M3-Washer018
M3-Washer019
M3x14-Screw002
M3x14-Screw003
M3x4-HeatSet
M3x4-HeatSet001
wire-mounter002
M3-Washer025
M3-Washer026
M3x14-Screw
M3x14-Screw004
M3-HeatSet
M3x8-Screw
z-rail-block-mount-right-counter-weight
M3x25-Screw
M3x25-Screw001
M4-Nut

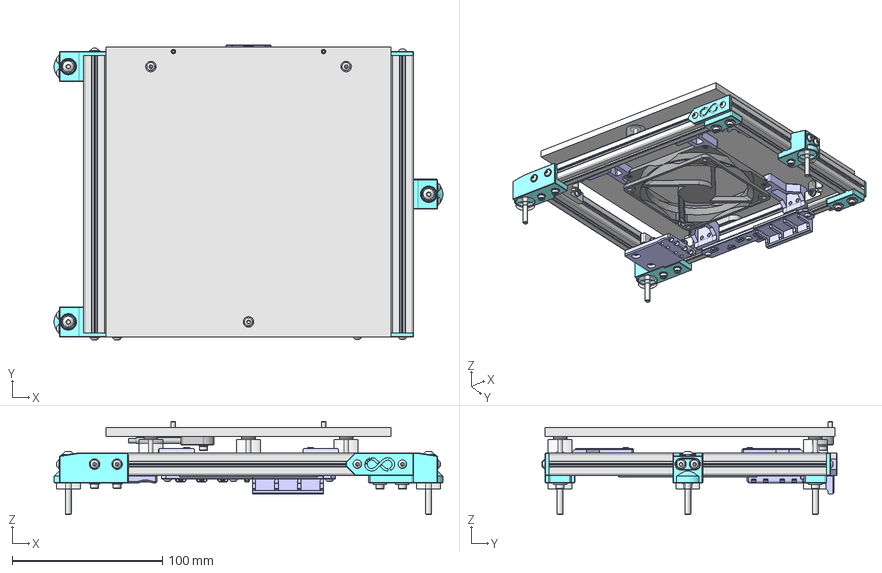
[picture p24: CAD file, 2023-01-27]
WIP/component-assembly/bed-assembly.FCStd
259.0 x 196.7 x 62.1 mm
front-left-arm
O-ring-10ODx4IDx2H001
silicon-spacer-16ODx4UDx9H001
M3-Washer
M3-Washer038
M3x10-Screw021
M3x10-Screw
M3-Washer044
M3-Washer045
M3x8-Screw004
M3x8-Screw005
M4-OD10-Washer-001
M4x40-Screw
M3-Washer052
M3-Washer053
M3x20-Screw
M3x20-Screw001
back-left-arm
silicon-spacer-16ODx4UDx9H002
O-ring-10ODx4IDx2H002
M3-Washer042
M3-Washer043
M3x10-Screw023
M3x10-Screw022
M3-Washer048
M3-Washer049
M3x8-Screw007
M3x8-Screw006
M4-OD10-Washer
M4x40-Screw001
M3-Washer055
M3-Washer054
M3x20-Screw003
M3x20-Screw002
middle-right-arm
silicon-spacer-16ODx4UDx9H003
O-ring-10ODx4IDx2H003
M3-Washer041
M3x10-Screw024
M4-OD10-Washer001
M4x40-Screw002
M3-Washer057
M3-Washer058
M3x20-Screw004
M3x20-Screw005
1515-185mm001
1515-190mm001
1515-185mm003
1515-190mm003
HBLTBS008
HBLTBS007
HBLTBS010
HBLTBS009
extrusion-connector
extrusion-connector001
M3-Washer018
M3-Washer019
M3-Washer022
M3-Washer021
M3-Washer023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

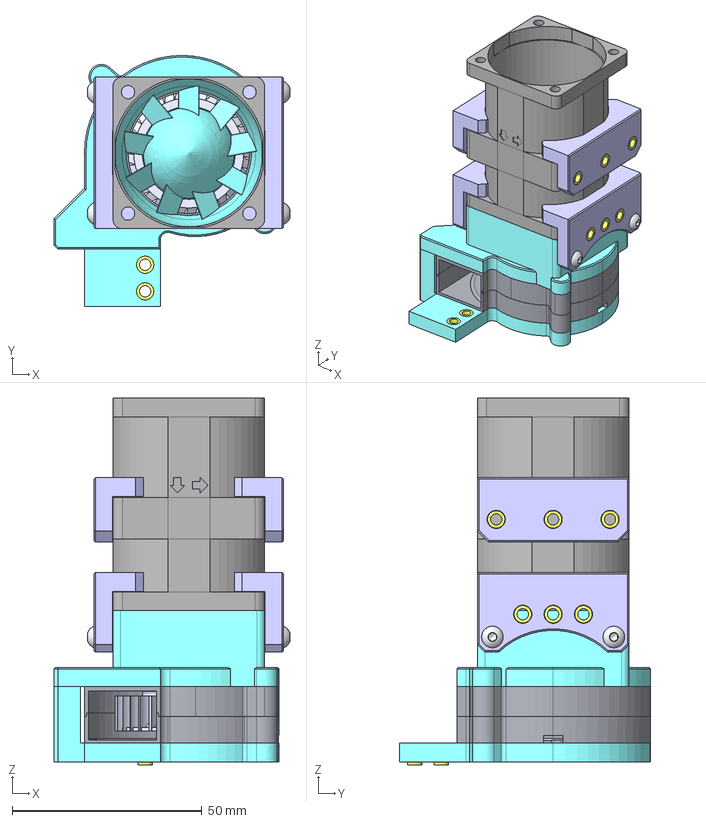
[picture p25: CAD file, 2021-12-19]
WIP/testing/4056-mackerel-compressor-assembly.FCStd
62.2 x 66.2 x 96.7 mm
fan-clamp001
fan-clamp
compressor-back-plate
turbine
top
bottom
bottom001
M3-HeatSet
M3-HeatSet001
M3-HeatSet002
M3-HeatSet003
M3-HeatSet004
M3-HeatSet005
M3-HeatSet006
M3-HeatSet007
M3-HeatSet008
M3-HeatSet009
M3-HeatSet010
M3-HeatSet011
M3x8-Screw
M3x8-Screw001
M3x8-Screw002
M3x8-Screw003
GDSTIME-top-plate
delta-4056-GFM0412SS
top-clamp
top-clamp001
M3-HeatSet012
M3-HeatSet013
M3-HeatSet014
M3-HeatSet015
M3-HeatSet016
M3-HeatSet017

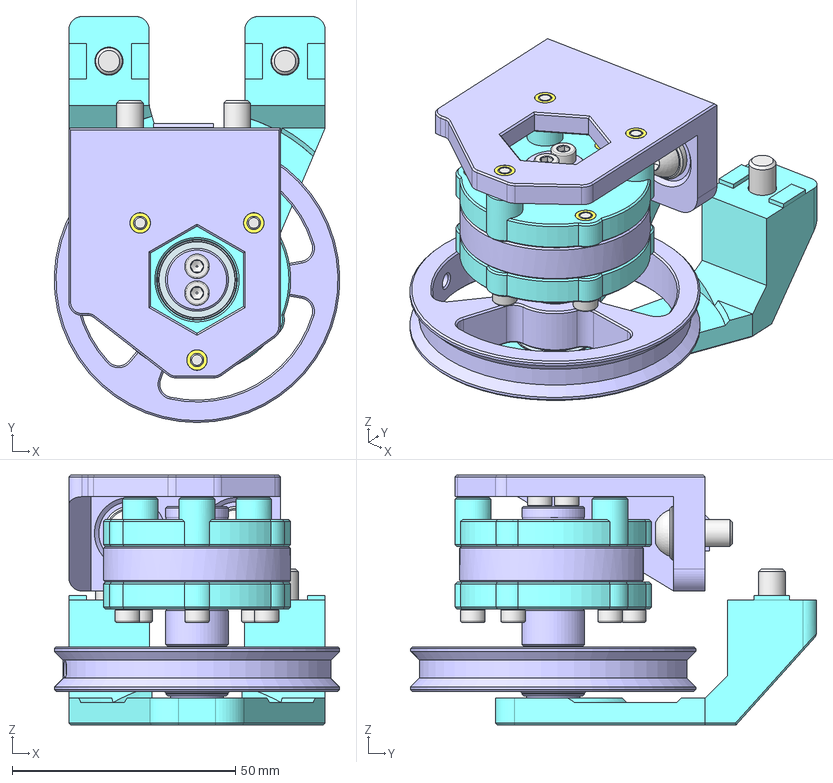
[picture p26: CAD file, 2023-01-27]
WIP/component-assembly/counter-weight-spring-box-assembly.FCStd
64.0 x 91.0 x 56.0 mm
cw-pulley-r30
bearing-6701ZZ1
cw-mid-plate
cw-axis
cw-front-plate
cw-back-plate
bearing-6701ZZ2
cw-spacer
bearing-6701ZZ
cw-front-mounter
cw-back-mounter
M3x4-HeatSet
M3x4-HeatSet001
M3x4-HeatSet002
M3x4-HeatSet003
M3x4-HeatSet004
M3x4-HeatSet005
M3x4-HeatSet006
M3x4-HeatSet007
M3x20-Screw
M3x20-Screw003
M3x20-Screw004
M3x30-Screw
M3x30-Screw003
M3x30-Screw004
M3x45-Screw
M3x45-Screw001
M6-Washer
M6-Washer001
M6x14-Screw
M6x14-Screw001
M6x14-Screw002
M6x14-Screw003

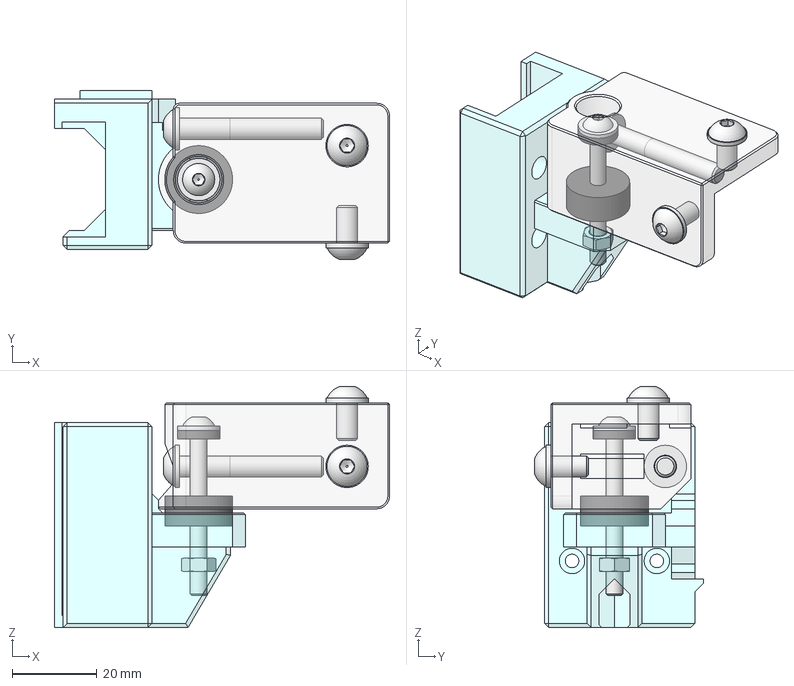
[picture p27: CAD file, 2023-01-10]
WIP/component-assembly/silicon-arm-assembly-tmp.FCStd
79.0 x 39.9 x 56.9 mm
rail-arm-fdm002
silicon-spacer-9mm-height001
M4-Nut001
silicon-spacer-10x4x003
m4x10x1-washer001
M4x40-Screw001
M5-Washer
M5x10-Screw
M5-Washer003
M5-Washer004
M5x10-Screw001
M5x35-Screw

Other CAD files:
CAD/v1-180-assembly.FCStd
WIP/component-assembly/ab-x-motor-assembly.FCStd
WIP/component-assembly/ab-y-motor-assembly.FCStd
WIP/component-assembly/x-endstop-flag-assembly.FCStd
2023-Nov-28th-patch/new-front-idler/A_2x_idler-housing.stl
2023-Nov-28th-patch/new-front-idler/M_1x_extruder-back-plate-no-tensioner.stl
2023-Nov-28th-patch/new-front-idler/M_2x_front-idler-mounter.stl
2023-Nov-28th-patch/new-front-idler/M_2x_rail-stopper.stl
2023-Nov-28th-patch/new-front-idler/front-idler-align-jig.stl
2023-Nov-28th-patch/new-front-idler/front-idler-align-jig_FOR_OLD_SHORT_FRAME.stl
BETA1_Release/STLs/Z-axis/1x_z-rail-block-mount-right.stl
BETA1_Release/STLs/Z-axis/2x_z-rail-block-mount-left.stl
BETA2_Release/STLs/Z-axis/bed-frame-1515/top-arm-threaded-ball-coupler/3x_spacer.stl
BETA2_Release/STLs/Z-axis/bed-frame-2020/top-arm-threaded-ball-coupler/3x_spacer.stl
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

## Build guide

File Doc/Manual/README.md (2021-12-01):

# Manual

- [Bed and extrusion drilling](./bed-extrusion.md)
- [How to print the parts](./printing.md)
- [Build log/assembly manual](./build-log.md)
- [EVA2 toolhead system "compatible"](./eva2.md)
- [tuning](./tuning.md)

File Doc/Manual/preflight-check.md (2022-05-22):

# Pre-flight check

## 0. Firmware config

- This config check is based on config of my machine(180mm). You will need to edit the config based on how you do the wiring and your hardwares. If not sure, please ask in #build-help or #firmware discord channel.
- sample config available at [sample config directory](https://github.com/ChipCE/SnakeOil-XY/tree/master/Firmware/sample-configs/Klipper/BTT_octopus_pro_Chip)

### 0.1. SONOFF config

If you are using sonoff wifi to control the power of the machine, there will be some extra step needed.

- Flash custom tasmota firmware following [tasmota firmware document](https://tasmota.github.io/docs/Getting-Started/)
- After installed custom fw, connect the sonoff module to wifi and remember it's IP address(Some other configs lie password, device name can also editable via SONOFF web interface).
- Enable firmware option26 by visit the following address using web browser <code>http://YOUR_SON_OFF_IP_HERE/cm?cmnd=SetOption26 ON</code>
- Add the following config into moonraker.conf
<pre>[power PSU]
type: tasmota
locked_while_printing: True
restart_klipper_when_powered: True
restart_delay: 5
address:YOUR_SONOF_IP_HERE
password:YOUR_SONOFF_PASSWORD</pre>
- After adding the config and restart moonraker/refresh webUI, you will have new section to turn the printer ON/OFF from fluidd/mainsail interface.

## 1. Endstop

- Move the toolhead to center position and execute <code>QUERY_ENDSTOPS</code> command. Both X and Y endstop status should be OPEN.
- Move the toolhead to touch X limit switch and execute <code>QUERY_ENDSTOPS</code> command. X endstop status should be TRIGGERED.
- Move the toolhead to touch Y limit switch and execute <code>QUERY_ENDSTOPS</code> command. Y endstop status should be TRIGGERED.
- Follow klipper guide to check bltouch. [Bltouch guide](https://www.klipper3d.org/BLTouch.html)

## 2. Motors

### 2.1. Motor location

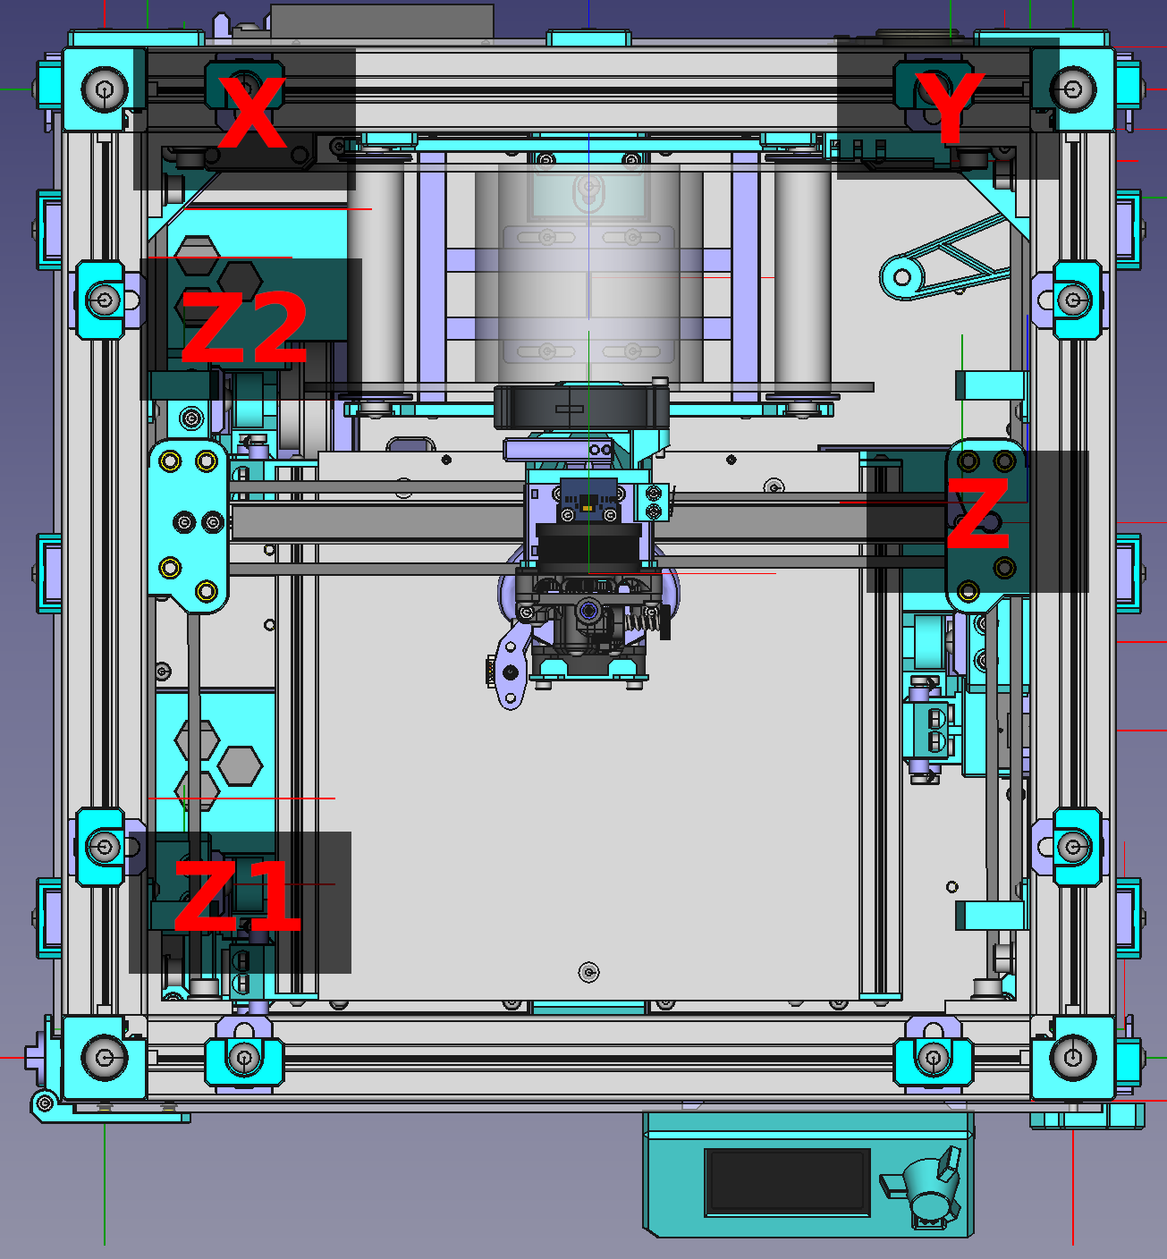
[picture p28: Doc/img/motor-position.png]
motor-position


- Run <code>STEPPER_BUZZ STEPPER=stepper_name_here</code> to verify the config and motor position are matched.

### 2.2 Motor direction and homing

- Move the toolhead to the center position, the bed to the middle position.
- Execute <code>G28 X</code>, the toolhead should move to the right, if not edit the <code>dir_pin</code> config and try again.
- Execute <code>G28 Y</code>, the toolhead should move to the back, if not edit the <code>dir_pin</code> config and try again.
- After homing X and Y worked, execute <code>G28</code> to home all axis. The homing order should be: Bed move down 10mm, home X, home Y, home Z

## 3. Bed position

- To make sure the bed leveling accuracy and does not take too much tries to level, the center of the bed should be well configured.
- Use some kind of marker or tape to make the center position of the bed. The bed center point is 85mm from the left edge of the bed and 85 mm from the front.
- Home all axis and execute <code>G1 X85 Y85</code>, if the nozzle is not directly above the center point of the bed, you will need to adjust the <code>position_endstop</code> of stepper_x and stepper_y section.

## 4. Probe offset, bed mesh and leveling

### 4.1. Probe offset(PROBE_CALIBRATE)

- Home axis and move the toolhead to the center of build plate.
<pre>G28
G0 X90 Y90
</pre>
- Start PROBE_CALIBRATE with <code>PROBE_CALIBRATE</code> command.
- Use <code>TESTZ Z=+ENTER_DISTANCE_HERE</code> or <code>TESTZ Z=-ENTER_DISTANCE_HERE</code> to move the nozzle up/down until it touch the bed surface. (Example : <code>TESTZ Z=-0.05</code>)
- Send command <code>ACCEPT</code> to accept the calibration result.
- Send command <code>SAVE_CONFIG</code> to save the above value.

### 4.2 Bed mesh and leveling

- Home all axis
- Verify if <code>Z_TILT_ADJUST</code> works.
- Verify if <code>BED_MESH_CALIBRATE</code> works.

## 5. Pid

- Do pid tuning for hotend and the bed. If you have fan under the bed, make sure to turn it on before do the bed pid tuning. If the fan is too strong, you will have to lower the fan max speed.

## 6. Slicer config

- My config using custom start gcode that parse the print area and filament type variable for "bed-mesh on print a rea only" and filament specified setting. Check <code>SET_FILAMENT_PROFILE</code> macro for more info.

### 6.1. Cura slicer gcode setting

\*start gcode

<pre>START_PRINT EXTRUDER_TEMP={material_print_temperature_layer_0} BED_TEMP={material_bed_temperature_layer_0} AREA_START=%MINX%,%MINY% AREA_END=%MAXX%,%MAXY% FILAMENT_TYPE={material_type}</pre>

\*end gcode

<pre>END_PRINT</pre>

- Cura slicer will also need custom post processing script. The script is available in Slicer/Cura/scripts/ directory. You will need to copy this file to scripts folder of cura (Cura "help" menu -> "Show configuration folder") and enable it in post-processing setting.
- Sample profiles also available at Slicer/Cura/profile/ directory

### 6.2. Prusa slicer setting

\*start gcode

<pre>START_PRINT EXTRUDER_TEMP=[first_layer_temperature] BED_TEMP=[first_layer_bed_temperature] AREA_START={first_layer_print_min[0]},{first_layer_print_min[1]} AREA_END={first_layer_print_max[0]},{first_layer_print_max[1]} FILAMENT_TYPE={filament_type[0]}</pre>

\*end gcode

<pre>END_PRINT</pre>

\*after layer change gcode

<pre>DISPLAY_GCODE_PROGRESS TOTAL_LAYER=[total_layer_count] CURRENT_LAYER={layer_num+1} PROGRESS=0 REMAIN=00:00</pre>

### 6.3 SET_FILAMENT_PROFILE macro

- I use SET_FILAMENT_PROFILE macro to set flow rate and pressure advance for each type of filament. You will need to edit the macro to set your tuned flow rate and pressure advance parameter for each filament type. Or disable the macro and use filament setting from slicer config.

## Advance input shaper tunning

- Check [here](./advance-resonance-tuning.md) if you have ringing/ghosting problem.

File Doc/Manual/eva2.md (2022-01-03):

# EVA2.4 toolhead system "compatible"

- The printer designed to able to use most of extruders and hotends in EVA 2 eco system. Titan aero and Hemera are not supported due the head heavy and wide design will reduce the useable area of the bed.

## Common parts for extruder available at [E-axis stl](https://github.com/ChipCE/SnakeOil-XY/tree/master/BETA2_Release/STLs/E-axis/carrier-common)

- 1x_extruder-back-plate.stl
- 1x_extruder-front-plate.stl
- 1x_extruder-bottom-plate.stl
- 1x_duct-tri-horn.stl
- 1x_extruder-cable-support.stl
- 2x_extruder-belt-mounter.stl
- 2x_extruder-belt-clamp.stl
- 1x_bltouch-mount.stl
- 1x_extruder-cable-end-mounter.stl

## Compact Sherpa mini mount

- The Sherpa mini mounter of SnakeOilXY have about 16mm shorter filament path compare to standard EVA2 mount.
- The default extruder option modified version of [Annex Engineering's Sherpa mini](https://github.com/Annex-Engineering/Sherpa_Mini-Extruder). Extruder parts available at [sherpa-mini-extruder-mod Stl](https://github.com/ChipCE/SnakeOil-XY/tree/master/BETA2_Release/STLs/E-axis/sherpa-mini-extruder-mod) and require 1 [E3D collet clip](https://e3d-online.com/products/collet-clips-pack-of-2)
- This version of sherpa mini mounter only support 4 hotends. Copperhead, Mosquito, Dragon, Dragonfly BMO(use the same mounter as Dragon hotend) and Nova(Not tested). For v6 and other hotends, use [P-C-R's Sherpa Mini Mount](https://github.com/EVA-3D/contrib-extras/blob/main/docs/extruders/pcr-sherpa-mini.md) or [Official Eva2 Sherpa mini mount](https://main.eva-3d.page/drives/sherpa_mini/) instead.

## Other hotends, extruders, fan ducts support

- Other extruders, hotend specified mounters and fan ducts can be found at [EVA 2 page](https://main.eva-3d.page/)

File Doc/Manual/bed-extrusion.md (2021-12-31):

# Aluminum bed plate and extrusion drilling location

## Aluminum bed plate

- The hole diameter for m3 bolt hand bolt head need to be at least the same or slightly bigger than the size in the drawing (except the d2.6mm holes that need to be tapped). Those hole side are calculated to encounter thermal expansions of the bed plate.

### 180mm machine

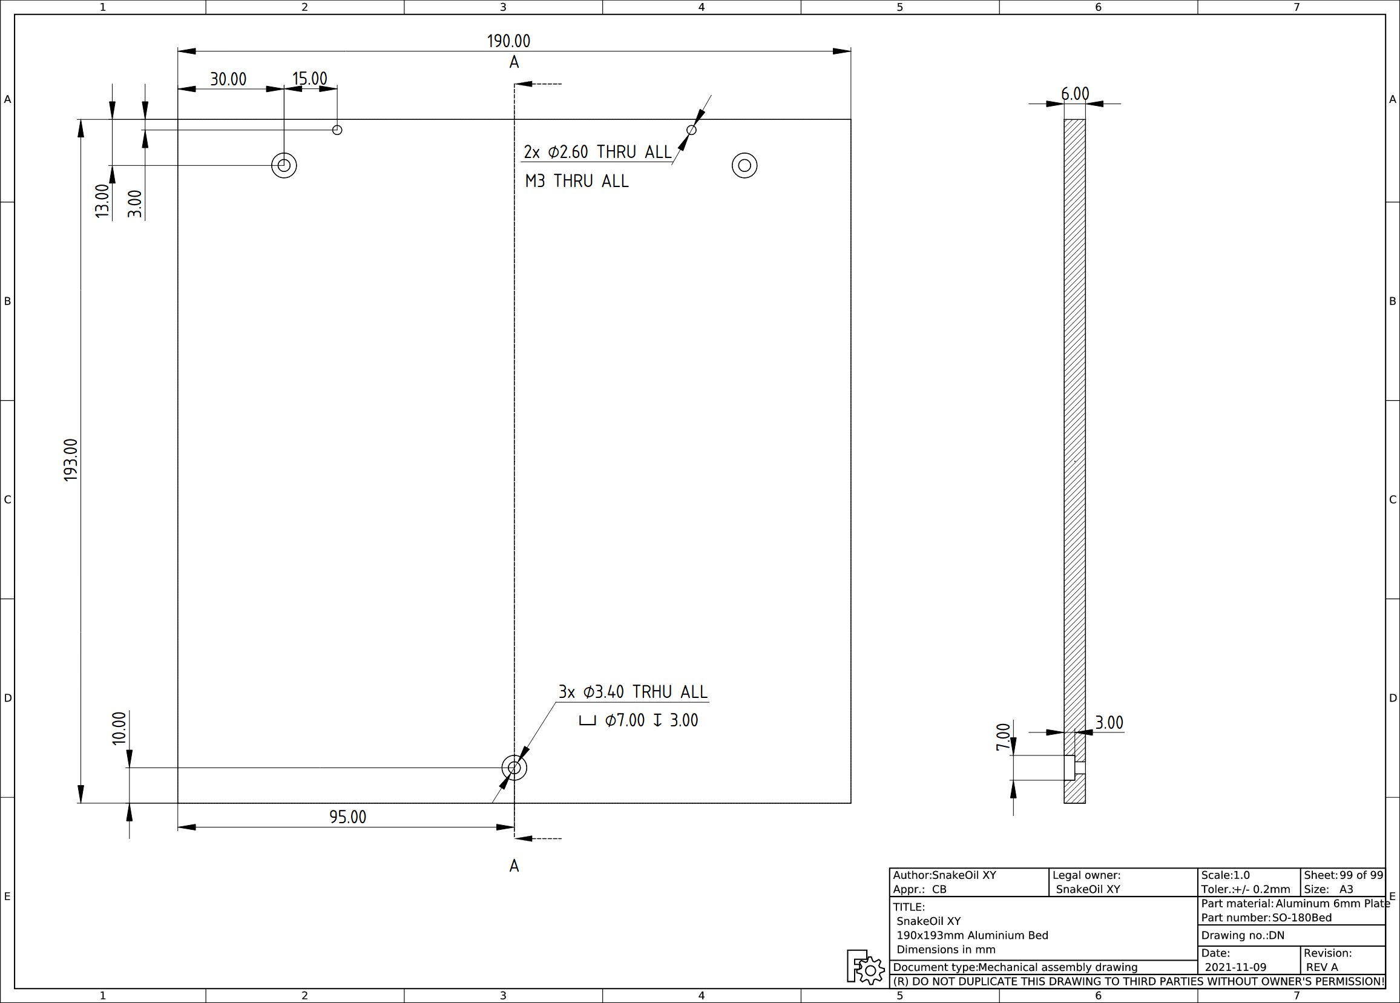
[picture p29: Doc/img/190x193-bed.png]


### 250mm machine

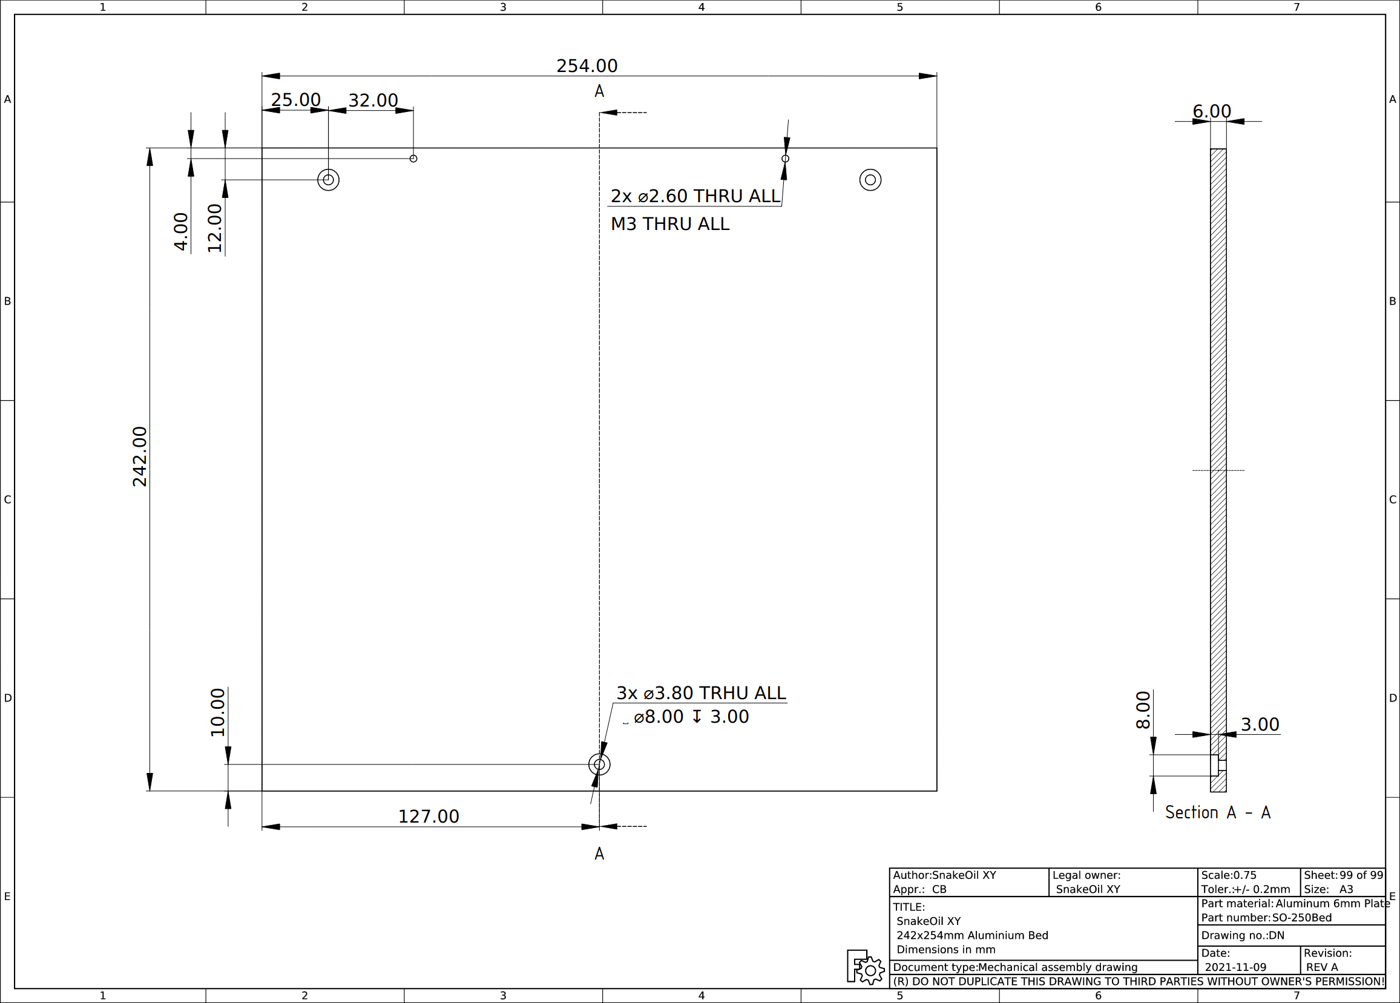
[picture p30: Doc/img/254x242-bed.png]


## Extrusion

- The hole diameter for 450/500/550mm extrusion is about 6.5~7.5mm (for m8 allen key access)
- The hole diameter for 280/330mm extrusion is about 6.5~7.5mm (for m6 allen key access)
- All extrusions will need to be M8 tapped.
- There are printable drilling jig and taping guide STLs in BETA2_Release/STLs/Tools/ directory.

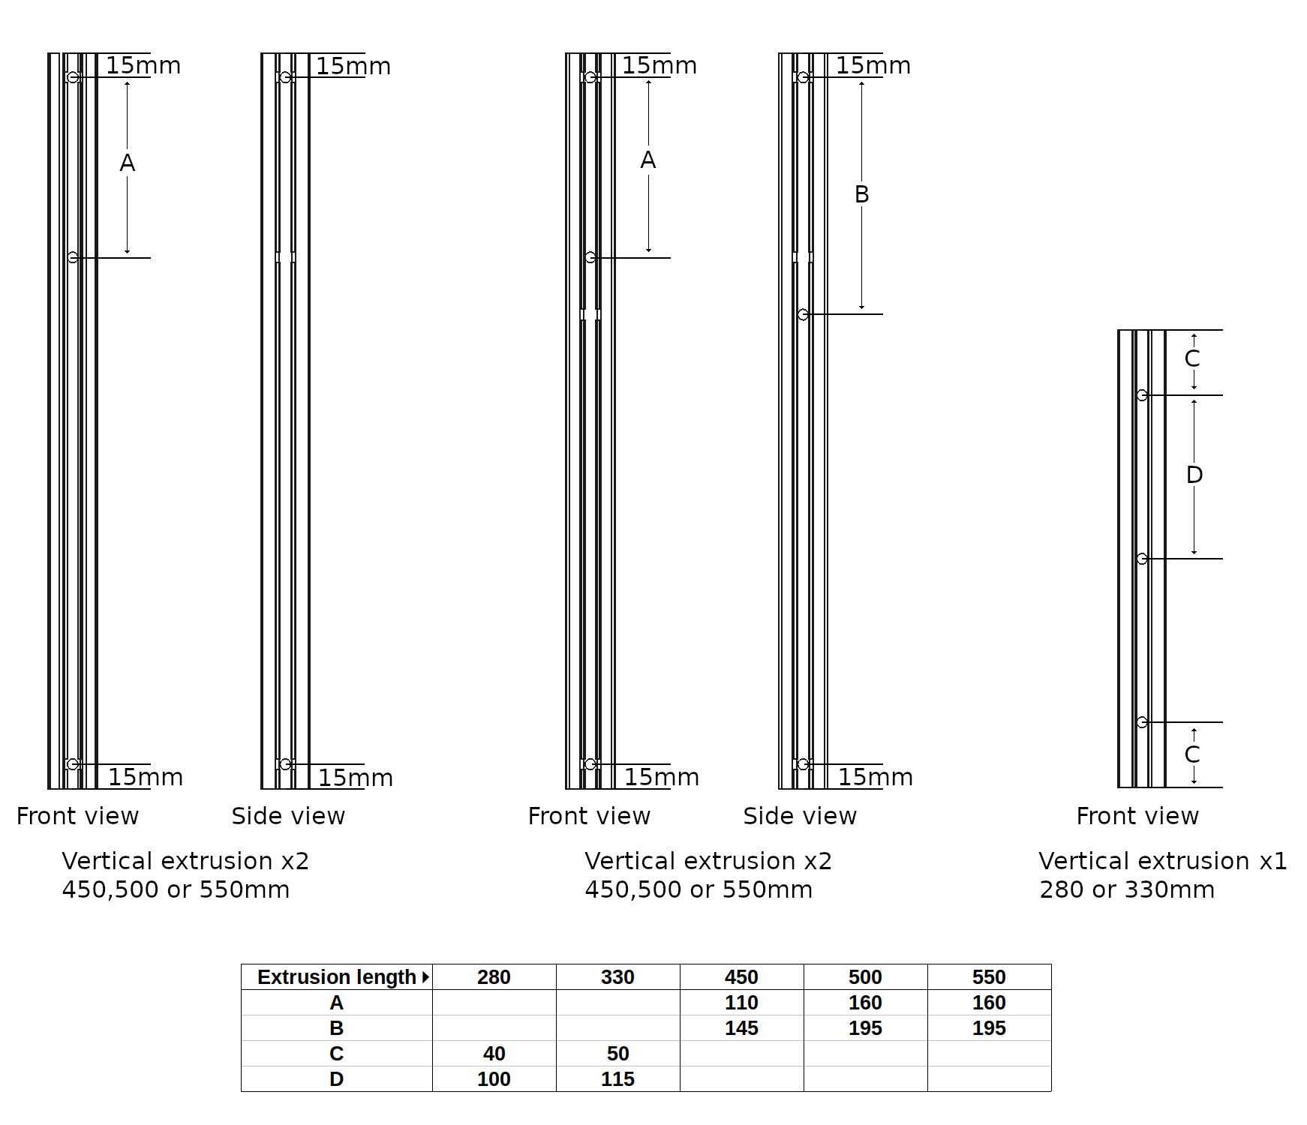
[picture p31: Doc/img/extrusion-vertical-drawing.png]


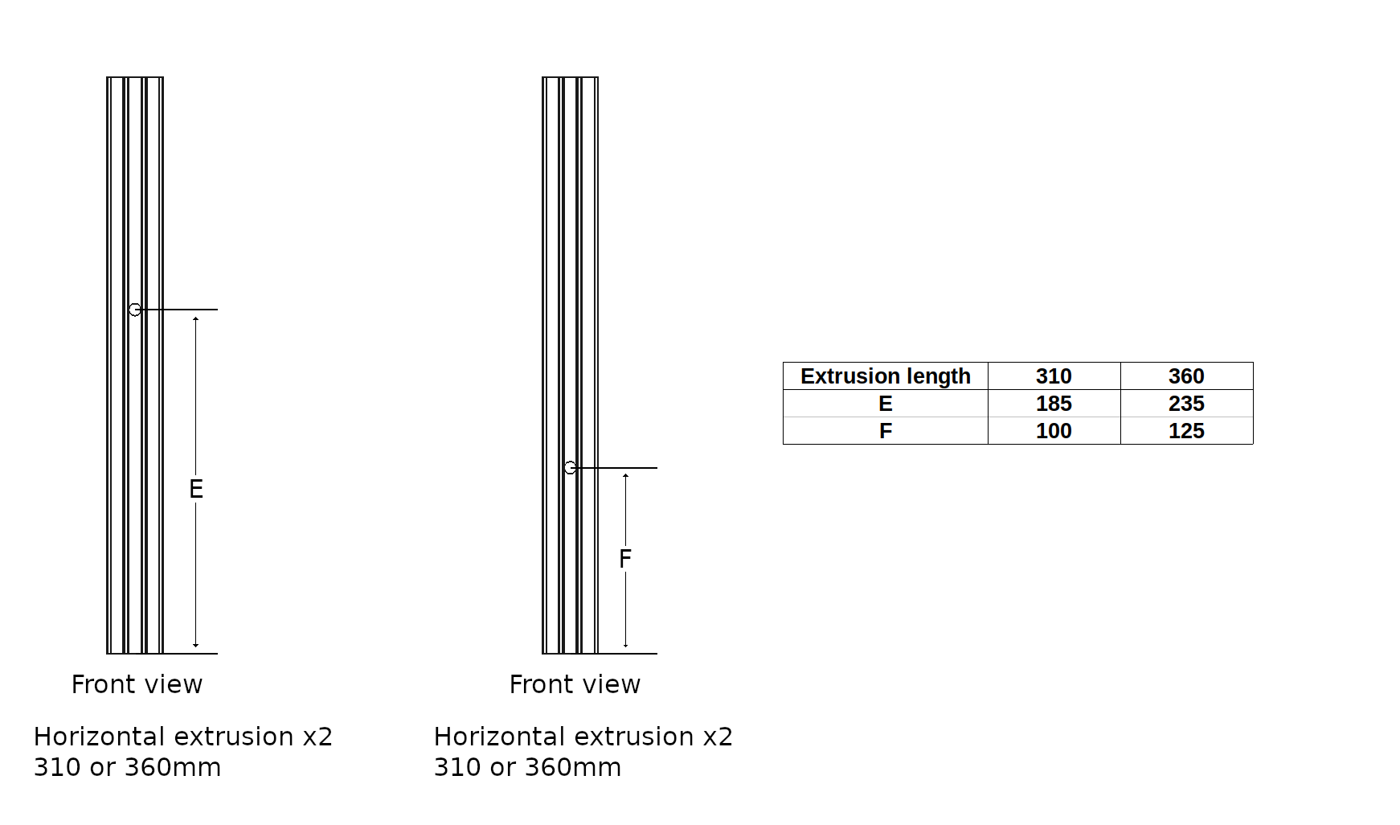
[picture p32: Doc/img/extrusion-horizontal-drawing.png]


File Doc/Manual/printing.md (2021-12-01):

# Print setting

## Slicer config

This is the setting I'm using but any other settings will work as long as the parts are strong enough.

<pre>Layer height : 0.2mm
Wall count : 5
Top/bottom layer : 5
Infill : 30% Gyroid 
Outer wall line width : 0.4mm
Inner wall line width : 0.45mm
Infill line width : 0.5mm
</pre>

## Filament

- In theory, PETG and higher temp-resistant filaments will work.
- Motor mount and tool head parts might require higher themp-resistant filament.
- If possible use strong filament for Z axis parts.
- Gillter or CF filled filaments might make the parts more brittle.

## Parts orientation

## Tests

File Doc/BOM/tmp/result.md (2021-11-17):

| Item | Quantity | Description |
| --- | --- | --- |
| 3030 M3-T-nut | 60 | |
| 3030 M5-T-nut | 10 | |
| 3030 M6-T-nut | 159 | |
| Big size M3-Washer | 16 | |
| Button head M10x25-Screw  | 4 | |
| Button head M3x10-Screw | 17 | |
| Button head M3x12-Screw | 8 | |
| Button head M3x16-Screw | 5 | |
| Button head M3x20-Screw | 1 | |
| Button head M3x30-Screw | 4 | |
| Button head M3x35-Screw | 2 | |
| Button head M3x6-Screw | 52 | |
| Button head M3x8-Screw | 3 | |
| Button head M4x25-Screw | 2 | |
| Button head M4x6-Screw | 4 | |
| Button head M5x10-Screw | 6 | |
| Button head M5x25-Screw | 3 | |
| Button head M5x40-Screw | 5 | |
| Button head M5x45-Screw | 1 | |
| Button head M5x50-Screw | 8 | |
| Button head M6x10-Screw | 17 | |
| Button head M6x12-Screw | 10 | |
| Button head M6x14-Screw | 17 | |
| Button head M6x16-Screw | 48 | |
| Button head M6x20-Screw | 4 | |
| Button head M6x25-Screw | 1 | |
| Button head M6x35-Screw | 6 | |
| Button head M8x12-Screw | 4 | |
| Button head M8x20-Screw | 26 | |
| Grub M3x8-Screw | 5 | |
| Grub M4x12-Screw | 3 | |
| Hex M3-Nut | 8 | |
| Hex M4-Nut | 2 | |
| Hex M5-Nut | 4 | |
| M3x10-Screw | 2 | |
| M3x3-HeatSet | 23 | |
| M3x4-HeatSet | 124 | |
| M3x5x4-HeatSet | 5 | |
| M4-HeatSet | 3 | |
| M5-HeatSet | 8 | |
| Small size M3-Washer | 71 | |
| Small size M5-Washer | 2 | |
| Socket head M2.5x12-Screw | 2 | |
| Socket head M3x10-Screw | 105 | |
| Socket head M3x12-Screw | 15 | |
| Socket head M3x14-Screw | 18 | |
| Socket head M3x16-Screw | 25 | |
| Socket head M3x20-Screw | 2 | |
| Socket head M3x25-Screw | 9 | |
| Socket head M3x35-Screw | 9 | |
| Socket head M3x40-Screw | 15 | |
| Socket head M3x45-Screw | 3 | |
| Socket head M3x6-Screw | 6 | |
| Socket head M3x70-Screw | 6 | |
| Socket head M3x8-Screw | 57 | |
| Socket head M4x12-Screw | 3 | |
| Socket head M6x14-Screw | 56 | |
| Spring washer M3 | 60 | |
| Square M3-Nut | 30 | |
| Standard size M5-Washer | 4 | |
| Standard size M6-Washer | 91 | |

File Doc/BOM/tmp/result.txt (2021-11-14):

Heat Set Insert M3,153.5
ISO4762 Screw M3x35,9.0
ISO4762 Screw M3x40,15.0
ISO4762 Screw M3x70,6.0
ISO4762 Screw M3x8,43.0
ISO7090 Washer M6,178.0
ISO7380-1 Screw M3x12,8.0
ISO7380-1 Screw M5x10,6.0
ISO7380-1 Screw M6x14,17.0
ISO7380-1 Screw M6x16,48.0
ISO4762 Screw M3x12,15.0
ISO4762 Screw M3x45,3.0
ISO7092 Washer M3,125.0
ISO7380-1 Screw M5x25,3.0
ISO7380-1 Screw M6x35,6.0
ISO4762 Screw M3x10,46.0
ISO4762 Screw M3x14,18.0
ISO4762 Screw M3x16,25.0
ISO4762 Screw M3x25,9.0
ISO4762 Screw M3x5,6.0
Heat Set Insert M5,8.0
ISO7380-1 Screw M5x50,8.0
ISO4032 Nut M3,8.0
ISO4762 Screw M2.5x12,2.0
ISO4762 Screw M2x10,2.0
ISO4762 Screw M3x20,2.0
ISO4762 Screw M3x6,6.0
ISO4762 Screw M4x12,3.0
ISO7380-1 Screw M3x16,5.0
ISO7380-1 Screw M3x35,2.0
ISO7380-1 Screw M3x8,3.0
ISO7380-1 Screw M6x10,17.0
ISO7380-1 Screw M3x10,17.0
ISO7380-1 Screw M3x30,4.0
ISO7380-1 Screw M3x6,56.0
ISO4026 Screw M3x8,3.0
ISO7380-1 Screw M6x12,12.0
ISO7380-1 Screw M8x12,4.0
maunal,0.0
ISO7092 Washer M5,4.0
ISO7092 Washer M6,2.0
ISO7380-1 Screw M5x40,5.0
ISO7380-1 Screw M5x45,1.0
ISO7380-1 Screw M6x20,4.0
ISO4762 Screw M6x14,56.0
ISO7380-1 Screw M8x20,26.0
ISO7380-1 Screw M10x25,4.0
ISO4032 Nut M4,2.0
ISO7380-1 Screw M4x25,2.0
ISO7380-1 Screw M4x6,4.0
ISO7380-1 Screw M6x25,2.0
Heat Set Insert M4,6.0
ISO4026 Screw M3x10,2.0
ISO4026 Screw M4x12,3.0
ISO4762 Screw M4x10,1.0
ISO7092 Washer M4,2.0
ISO7093-1 Washer M3,35.0
ISO4762 Screw M2x6,8.0
ISO7089 Washer M6,2.0
ISO4032 Nut M5,4.0
ISO7089 Washer M5,8.0

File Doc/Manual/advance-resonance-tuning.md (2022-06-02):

# Advance resonance tuning

## 1. Introduction

As reported by some of our members, even with an inputshaper enabled, a ringing pattern is present on printed parts(check images bellow). I did some research and with the help of our members, we found a solution to this problem.

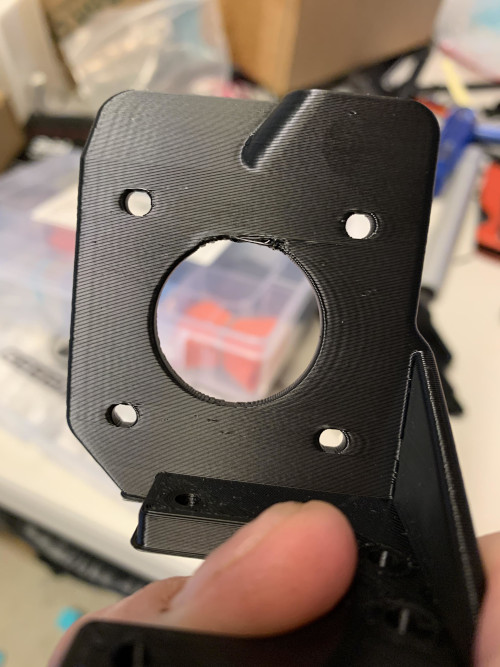
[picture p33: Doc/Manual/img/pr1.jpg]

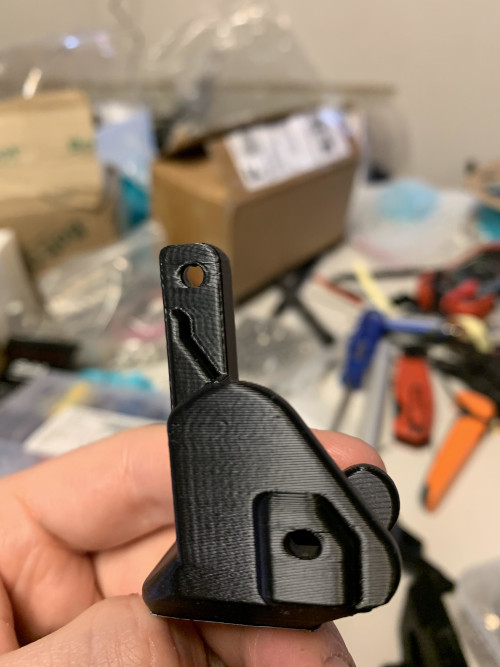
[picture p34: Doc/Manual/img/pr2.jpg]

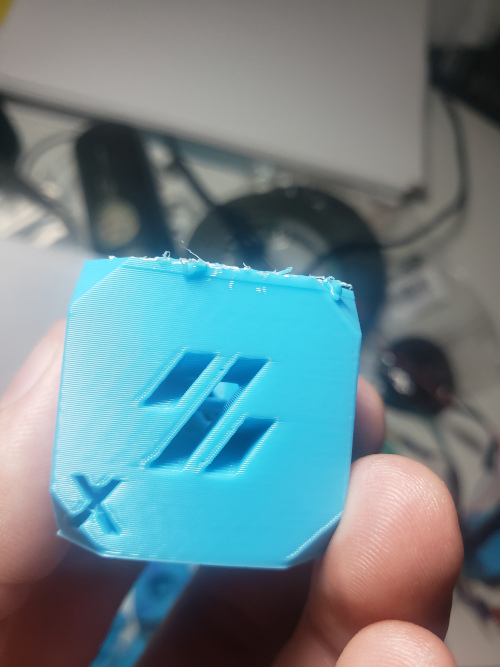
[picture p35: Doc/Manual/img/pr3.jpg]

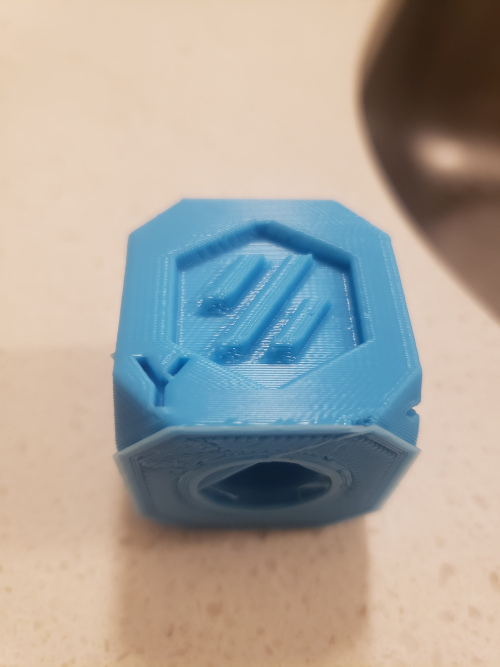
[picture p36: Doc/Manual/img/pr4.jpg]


## 2. Source of the problem

The acceleration sensor measures vibration of the toolhead, and applies shaper to reduce the vibration but assumes that the bed is rock solid (not affected by the toolhead or the printer vibrations).
Many things can falsify those tests: if your printer is placed on an unstable surface, has soft feet, the bed is able to vibrate or move or like in our case, the heavy bed is held by belts and they can stretch/shrink. The vibrations caused by the moving of the bed is, in our case, causing the ringing in the parts.

## 3. Solution

To eliminate the ringing, we need to measure vibrations of both the toolhead and the bed, then force the inputshaper to reduce the vibrations of both the bed and the toolhead. There are 2 methods to do this : <code>Use Klipper's calibrate_shaper with multy inputs</code> OR <code>manually calculate the shaper frequency</code>

※The image bellow is the Voron cube printed with 200mm/s outer wall after tuning with the second method.
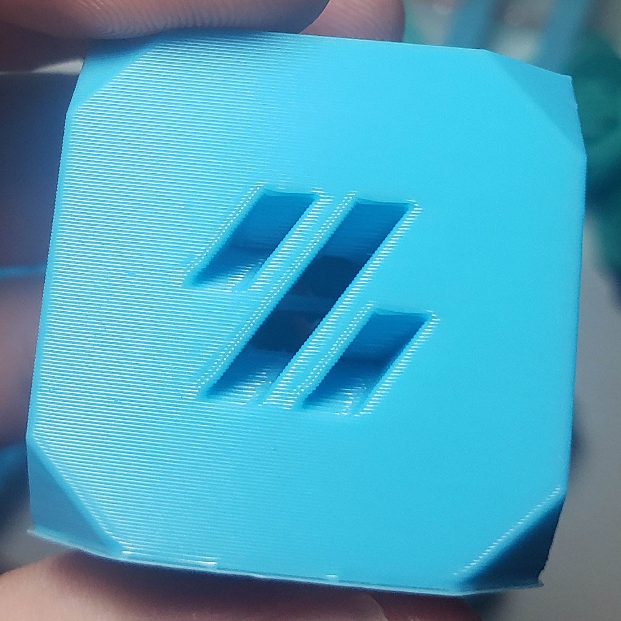
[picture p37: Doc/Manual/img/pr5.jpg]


## 4. Calculate the shaper frequency

### 4.1. Method 1 : Use Klipper's calibrate_shaper with multy inputs

- Make sure there are no <code>.csv</code> files left from previous calibration in <code>/tmp</code> directory. (tip : run <code>rm /tmp/\*.csv</code> to remove the old files if needed)
- Measure vibrations with the ADXL345 sensor mount on the toolhead. This step will generate 2 csv files (/tmp/resonances_x_yyyymmdd.csv and /tmp/resonances_y_yyyymmdd.csv)
- Measure the vibrations but with the ADXL345 sensor mount on the bed. This step will also generate 2 more csv files (/tmp/resonances_x_yyyymmdd.csv and /tmp/resonances_y_yyyymmdd.csv)
- Now you will have 4 csv files in <code>/tmp</code> directory,run the following commands, klipper will calculate the shaper frequency based on all 4 csv files we generated in the previous steps.

<pre>~/klipper/scripts/calibrate_shaper.py /tmp/resonances_x_*.csv -o /tmp/shaper_calibrate_x.png
~/klipper/scripts/calibrate_shaper.py /tmp/resonances_y_*.csv -o /tmp/shaper_calibrate_y.png
  </pre>

- Set the shaper frequency and shaper type as the above commands result.

### 4.2. Method 2 : Manually calculate the shaper frequency(if the above method does not work)

Each shaper has an effective range, all vibrations in that range will be reduced to a certain level. We measure the vibrations of the toolhead and the bed, then set a value that works for both. The only drawback to this method is that shapers with wide effective range like EI2 and EI3 will have lower recommended max accel value compared to other shaper.

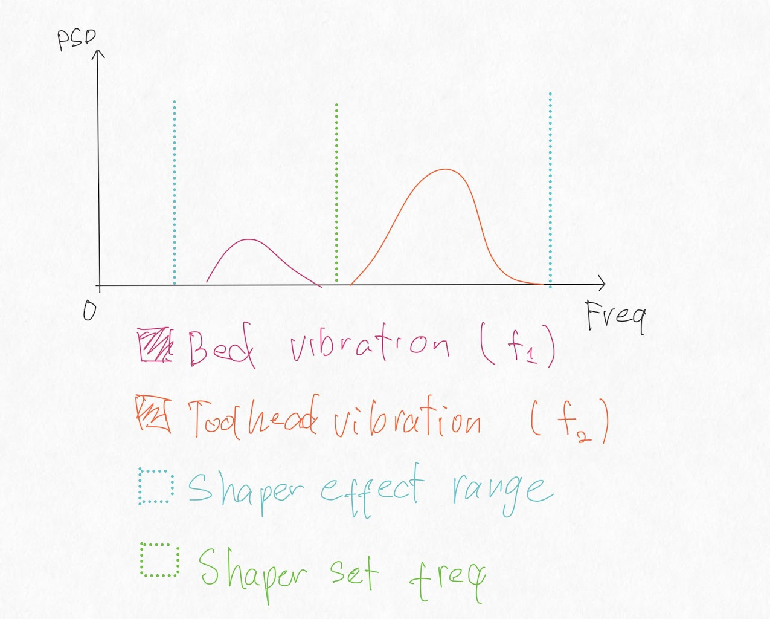
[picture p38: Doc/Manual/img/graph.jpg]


- Make sure there are no <code>.csv</code> files left from previous calibration in <code>/tmp</code> directory. (tip : run <code>rm /tmp/\*.csv</code> to remove the old files if needed)
- Measure vibrations with the ADXL345 sensor mount on the toolhead. This step will generate 2 csv files (/tmp/resonances_x_yyyymmdd.csv and /tmp/resonances_y_yyyymmdd.csv)
- Run the following commands to generate the graph of the toolhead vibration
<pre>~/klipper/scripts/calibrate_shaper.py /tmp/resonances_x_*.csv -o /tmp/shaper_calibrate_toolhead_x.png
~/klipper/scripts/calibrate_shaper.py /tmp/resonances_y_*.csv -o /tmp/shaper_calibrate_toolhead_y.png
  </pre>
- Remove the previous step data with the command bellow
<pre>rm /tmp/*.csv</pre>
- Measure the vibrations but with the ADXL345 sensor mount on the bed. This step will generate 2 csv files (/tmp/resonances_x_yyyymmdd.csv and /tmp/resonances_y_yyyymmdd.csv)
- Run the following commands to generate the graph of the bed vibration
<pre>~/klipper/scripts/calibrate_shaper.py /tmp/resonances_x_*.csv -o /tmp/shaper_calibrate_bed_x.png
~/klipper/scripts/calibrate_shaper.py /tmp/resonances_y_*.csv -o /tmp/shaper_calibrate_bed_y.png
  </pre>

- Download the [calc tool html file here](https://raw.githubusercontent.com/SnakeOilXY/SnakeOil-XY/master/Software/resonance-caculator/index.html) and open it with your web browser by double clicking the htlm file.
- Enter the measured results(from the generated graphs) into the calc tool and it will output the combined frequency that works for both the toolhead and the bed.
- Set that value in your printer config.

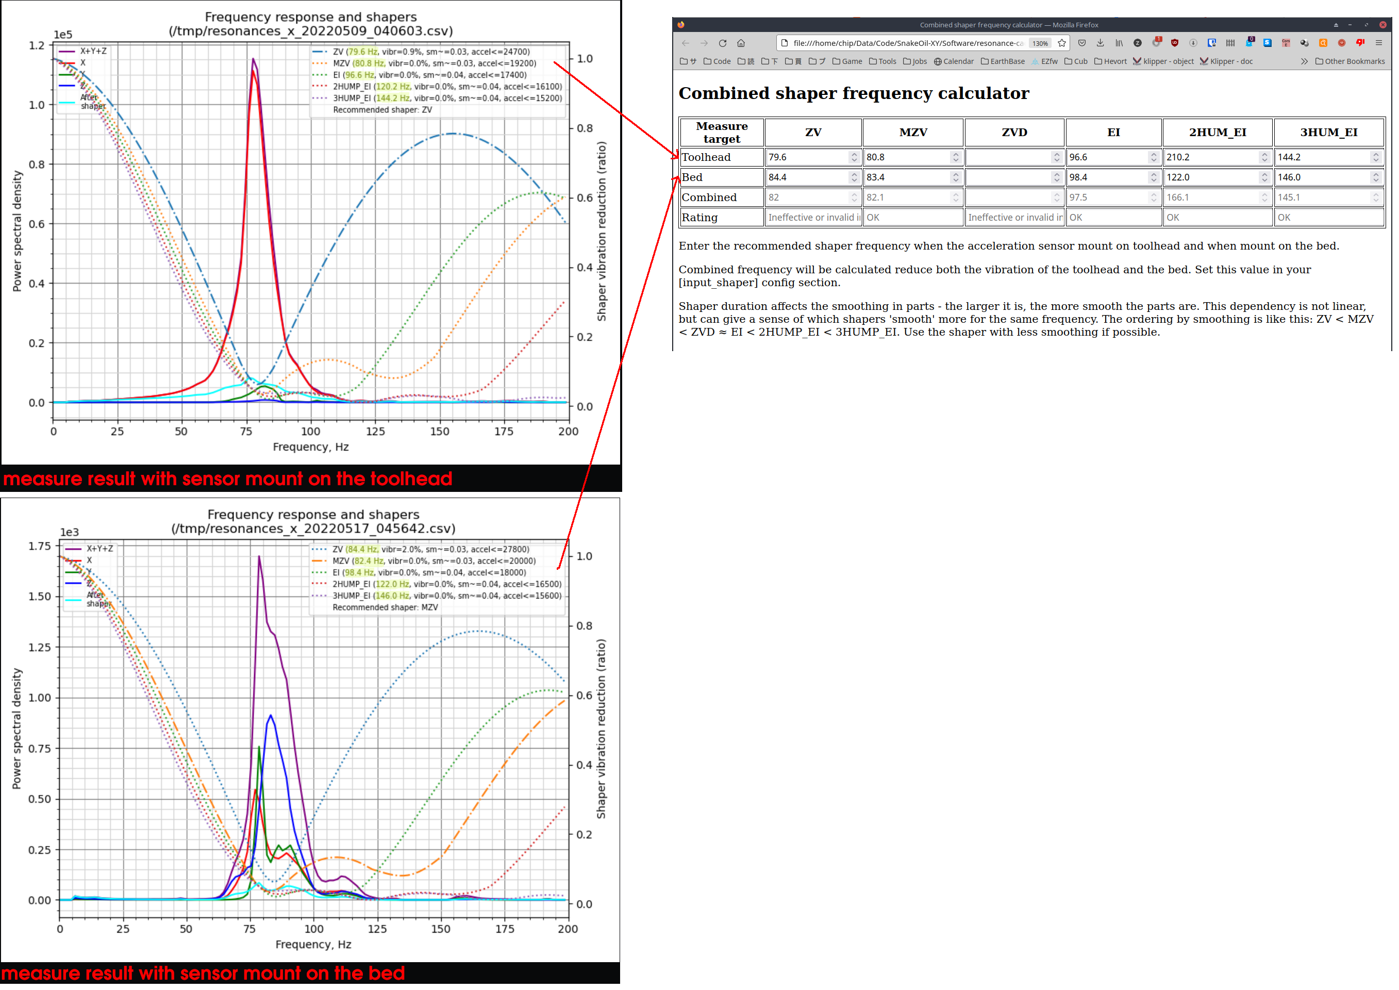
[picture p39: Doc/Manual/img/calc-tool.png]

※Example for the X axis

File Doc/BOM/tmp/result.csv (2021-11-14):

Heat Set Insert M3 | 153.5
Socket head Screw M3x35 | 9.0
Socket head Screw M3x40 | 15.0
Socket head Screw M3x70 | 6.0
Socket head Screw M3x8 | 53.0
Standard size Washer M6 | 180.0
Button head Screw M3x12 | 8.0
Button head Screw M5x10 | 6.0
Button head Screw M6x14 | 17.0
Button head Screw M6x16 | 48.0
Socket head Screw M3x12 | 15.0
Socket head Screw M3x45 | 3.0
Small size Washer M3 | 127.0
Button head Screw M5x25 | 3.0
Button head Screw M6x35 | 6.0
Socket head Screw M3x10 | 97.0
Socket head Screw M3x14 | 18.0
Socket head Screw M3x16 | 25.0
Socket head Screw M3x25 | 9.0
Socket head Screw M3x5 | 6.0
Heat Set Insert M5 | 8.0
Button head Screw M5x50 | 8.0
Hex Nut M3 | 8.0
Socket head Screw M2.5x12 | 2.0
Socket head Screw M2x10 | 2.0
Socket head Screw M3x20 | 2.0
Socket head Screw M3x6 | 6.0
Socket head Screw M4x12 | 3.0
Button head Screw M3x16 | 8.0
Button head Screw M3x35 | 2.0
Button head Screw M3x8 | 3.0
Button head Screw M6x10 | 17.0
Button head Screw M3x10 | 17.0
Button head Screw M3x30 | 4.0
Button head Screw M3x6 | 69.0
Grub Screw M3x8 | 5.0
Button head Screw M6x12 | 12.0
Button head Screw M8x12 | 4.0
Small size Washer M5 | 4.0
Small size Washer M6 | 2.0
Button head Screw M5x40 | 5.0
Button head Screw M5x45 | 1.0
Button head Screw M6x20 | 4.0
Socket head Screw M6x14 | 56.0
Button head Screw M8x20 | 26.0
Button head Screw M10x25 | 4.0
Hex Nut M4 | 2.0
Button head Screw M4x25 | 2.0
Button head Screw M4x6 | 4.0
Button head Screw M6x25 | 2.0
Heat Set Insert M4 | 6.0
Grub Screw M4x12 | 3.0
Big size Washer M3 | 35.0
Socket head Screw M2x6 | 8.0
Hex Nut M5 | 4.0
Standard size Washer M5 | 8.0
Spring washer M3 | 130.0
Square nut M3 for 1515 frame (hex nut also works) | 60.0
M6 T-nut | 162.0
M5 T-nut | 10.0
M4 T-nut | 0.0
M3 T-nut | 50.0

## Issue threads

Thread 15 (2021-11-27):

Various typos and spelling corrections

martinbudden, 2021-11-27:
I've spotted a couple of typos/spelling mistakes

In https://github.com/ChipCE/SnakeOil-XY/blob/master/Doc/Manual/printing.md:
`Gillter or CF filled filaments might make the parts more brite.`
presumably you mean "Glitter" and "brittle"?

You use the word `tunning` a few times. Presumably you mean `tuning`?

ChipCE, 2021-12-01:
Thank you!

Closed 2021-12-01.

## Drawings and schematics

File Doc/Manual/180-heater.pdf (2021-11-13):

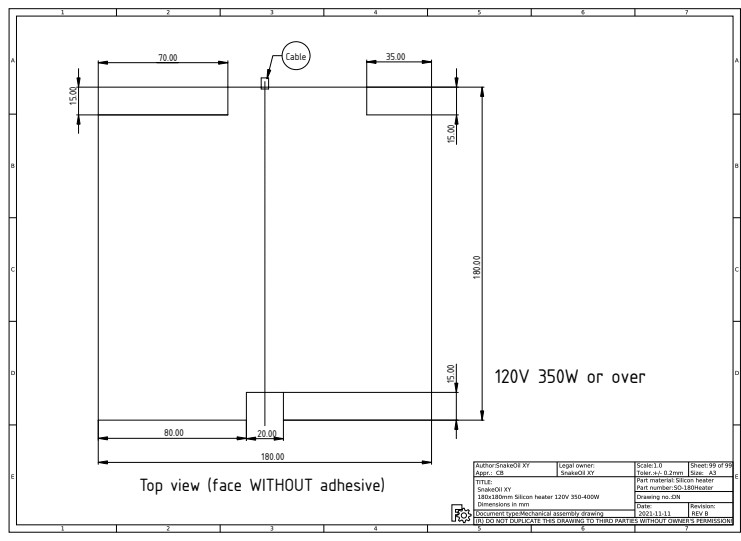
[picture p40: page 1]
Cable; 120V 350W or over

Top view (face WITHOUT adhesive)

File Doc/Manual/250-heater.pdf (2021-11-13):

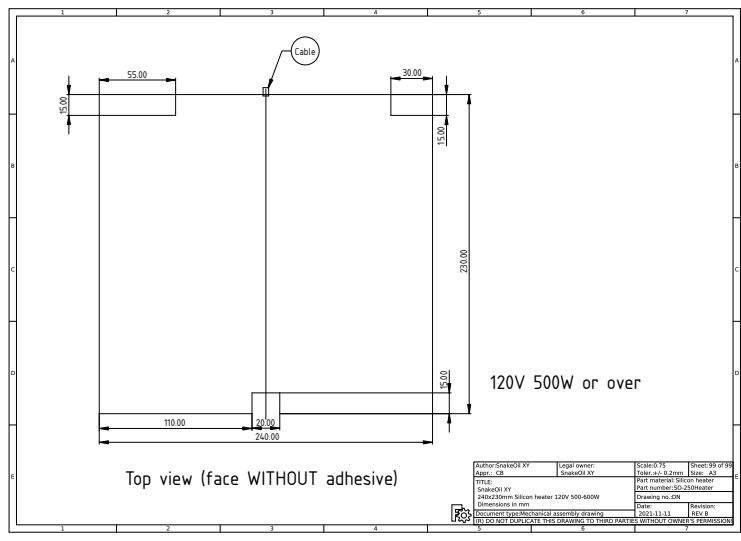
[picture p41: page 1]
Cable; 120V 500W or over

Top view (face WITHOUT adhesive)

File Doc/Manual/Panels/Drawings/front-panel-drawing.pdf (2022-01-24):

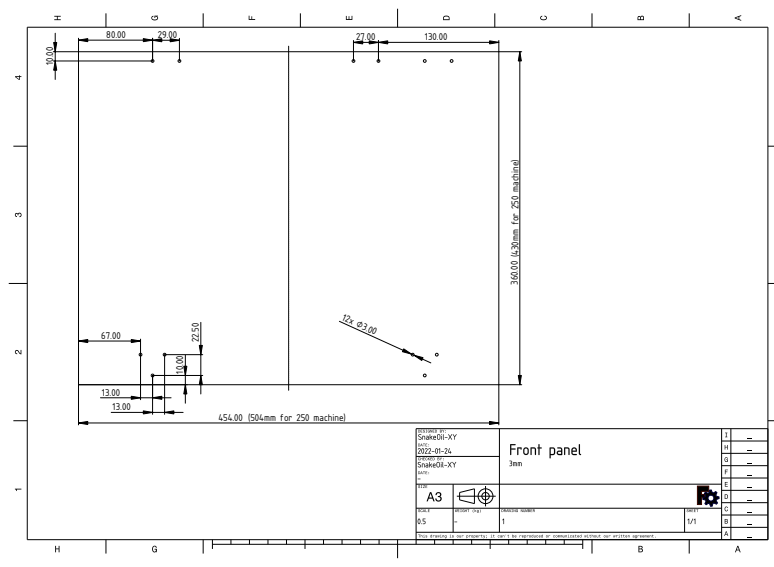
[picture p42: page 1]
(430mm for 250 machine); (504mm for 250 machine)

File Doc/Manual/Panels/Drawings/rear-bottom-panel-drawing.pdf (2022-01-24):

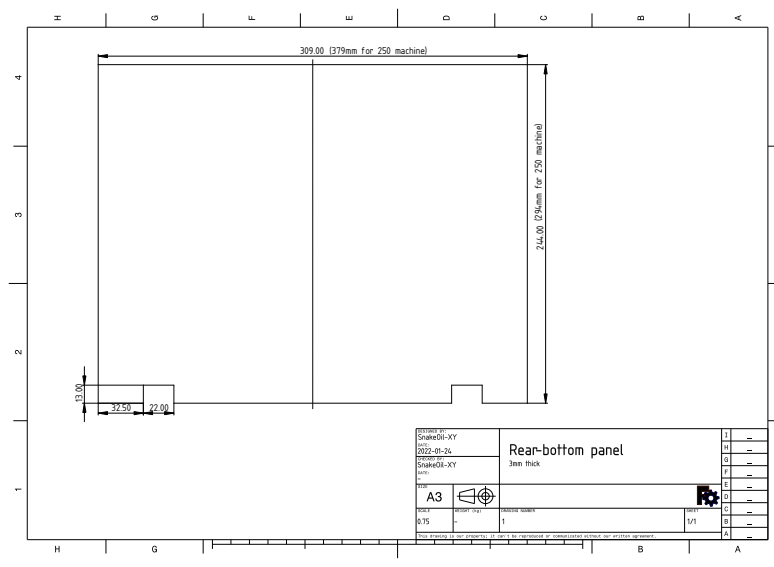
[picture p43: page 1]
(379mm for 250 machine); (294mm for 250 machine⁾

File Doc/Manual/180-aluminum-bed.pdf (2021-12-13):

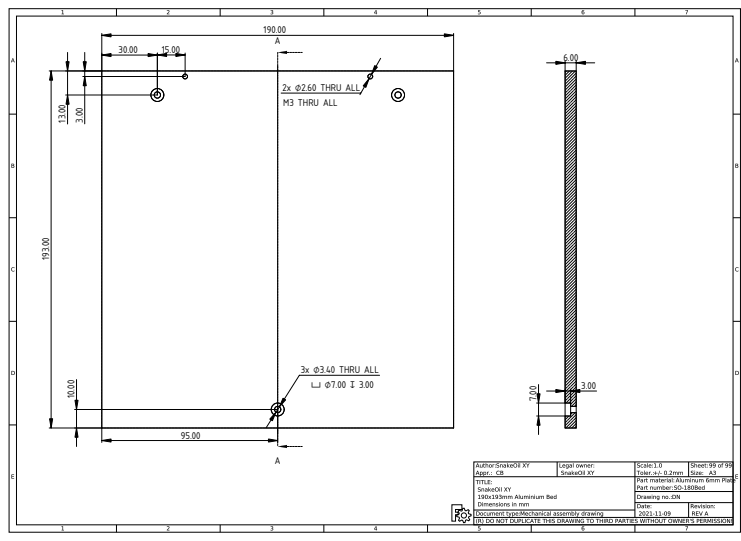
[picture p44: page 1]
2x ⌀2.60 THRU ALL; 3x ⌀3.40 THRU ALL; M3 THRU ALL

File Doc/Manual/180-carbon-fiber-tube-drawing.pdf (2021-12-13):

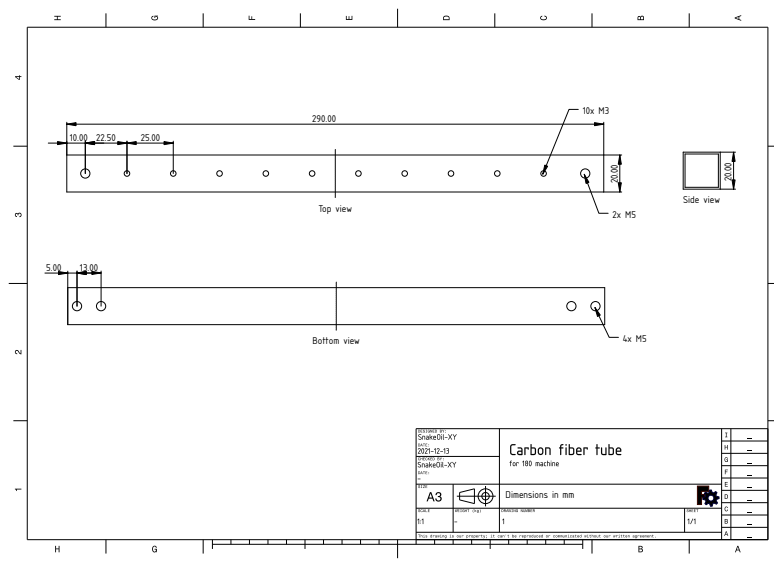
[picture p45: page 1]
Top view; Bottom view; Side view

Dimensions in mm

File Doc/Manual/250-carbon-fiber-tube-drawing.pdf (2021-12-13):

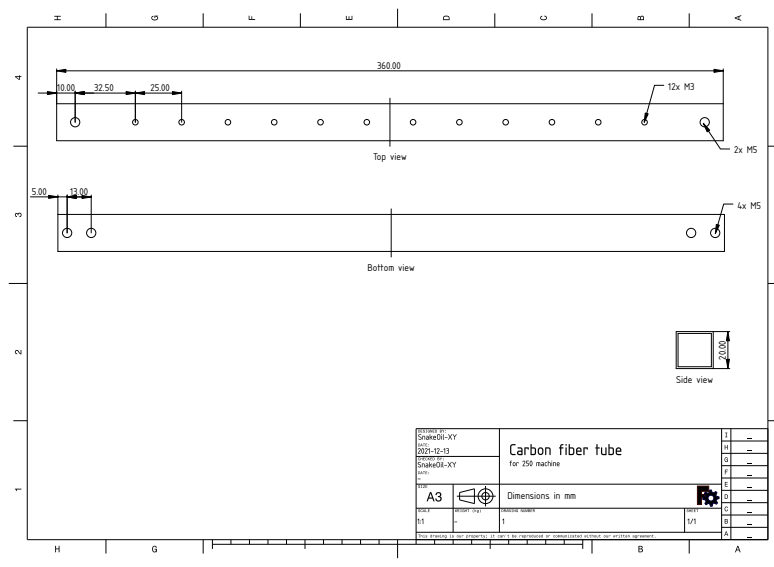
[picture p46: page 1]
Top view; Bottom view; Side view

Dimensions in mm

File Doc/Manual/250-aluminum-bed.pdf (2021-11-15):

A

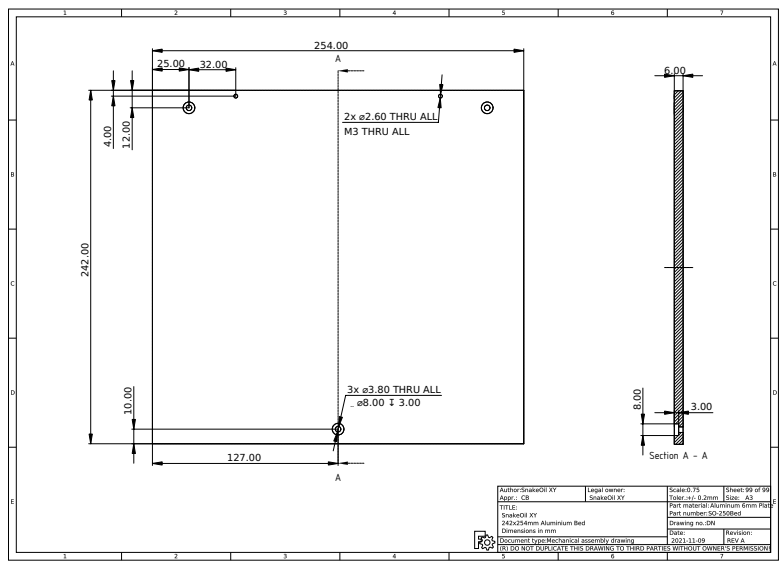
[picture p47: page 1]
3x ⌀3.80 THRU ALL; 2x ⌀2.60 THRU ALL; Section A - A; M3 THRU ALL

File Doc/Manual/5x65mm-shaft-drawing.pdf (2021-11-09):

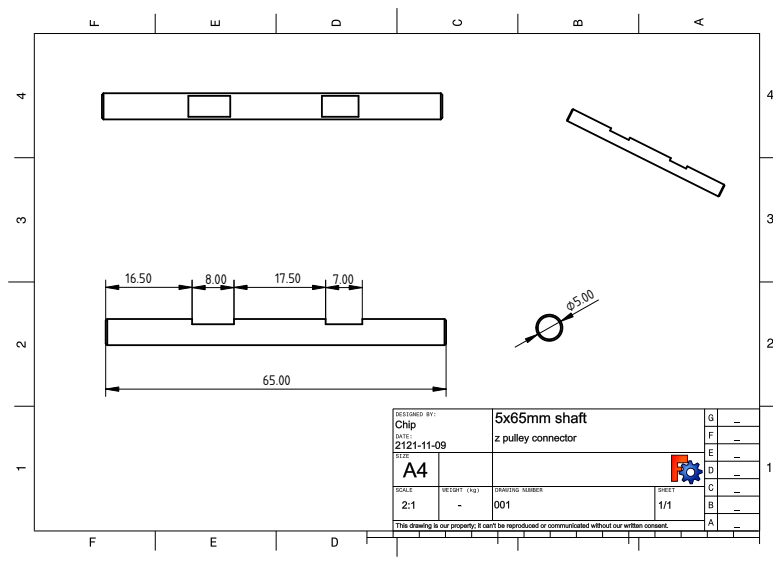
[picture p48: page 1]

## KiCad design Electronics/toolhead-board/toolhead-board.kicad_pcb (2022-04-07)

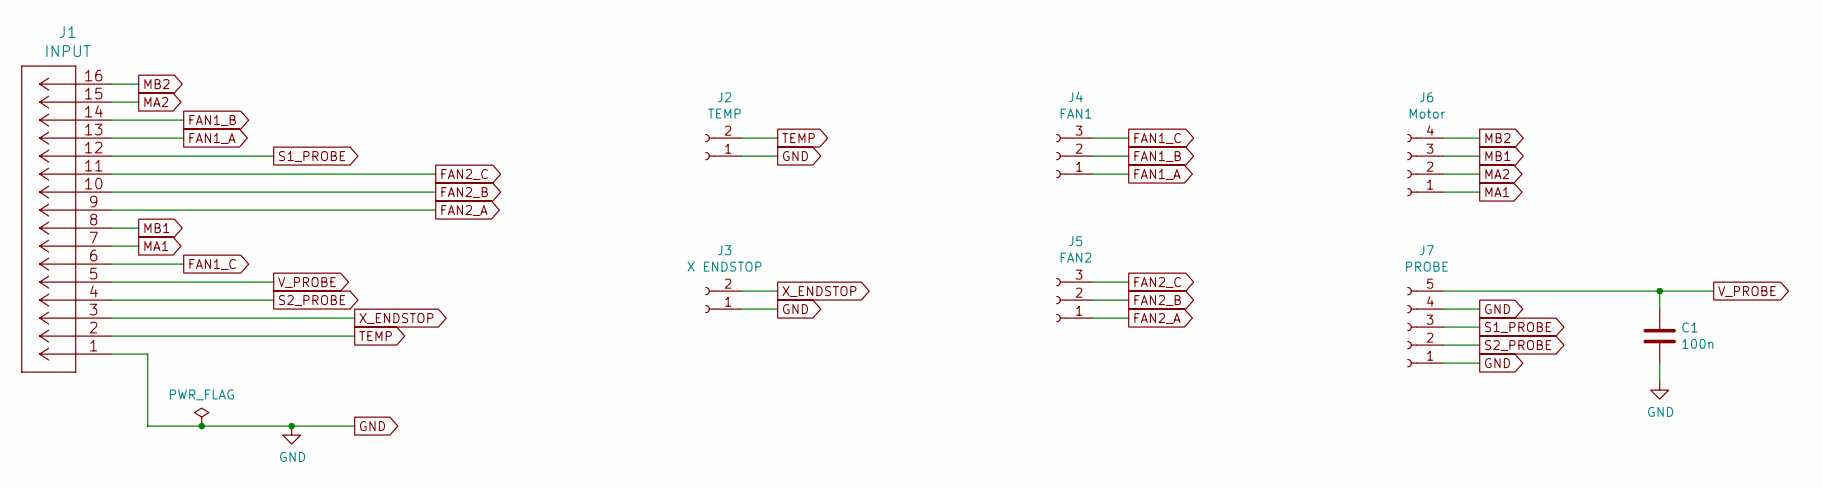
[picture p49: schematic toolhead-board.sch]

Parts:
C1: 100n; C_0805_2012Metric_Pad1.15x1.40mm_HandSolder
J1: INPUT; microfit-16
J2: TEMP; JST_XH_B02B-XH-A_1x02_P2.50mm_Vertical
J3: X ENDSTOP; JST_XH_B02B-XH-A_1x02_P2.50mm_Vertical
J4: FAN1; JST_XH_B03B-XH-A_1x03_P2.50mm_Vertical
J5: FAN2; JST_XH_B03B-XH-A_1x03_P2.50mm_Vertical
J6: Motor; JST_XH_B04B-XH-A_1x04_P2.50mm_Vertical
J7: PROBE; JST_XH_B05B-XH-A_1x05_P2.50mm_Vertical

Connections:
FAN1_A: J1.13, J4.1
FAN1_B: J1.14, J4.2
FAN1_C: J1.6, J4.3
FAN2_A: J1.9, J5.1
FAN2_B: J1.10, J5.2
FAN2_C: J1.11, J5.3
GND: C1.2, J1.1, J2.1, J3.1, J7.1, J7.4
MA1: J1.7, J6.1
MA2: J1.15, J6.2
MB1: J1.8, J6.3
MB2: J1.16, J6.4
S1_PROBE: J1.12, J7.3
S2_PROBE: J1.4, J7.2
TEMP: J1.2, J2.2
V_PROBE: C1.1, J1.5, J7.5
X_ENDSTOP: J1.3, J3.2

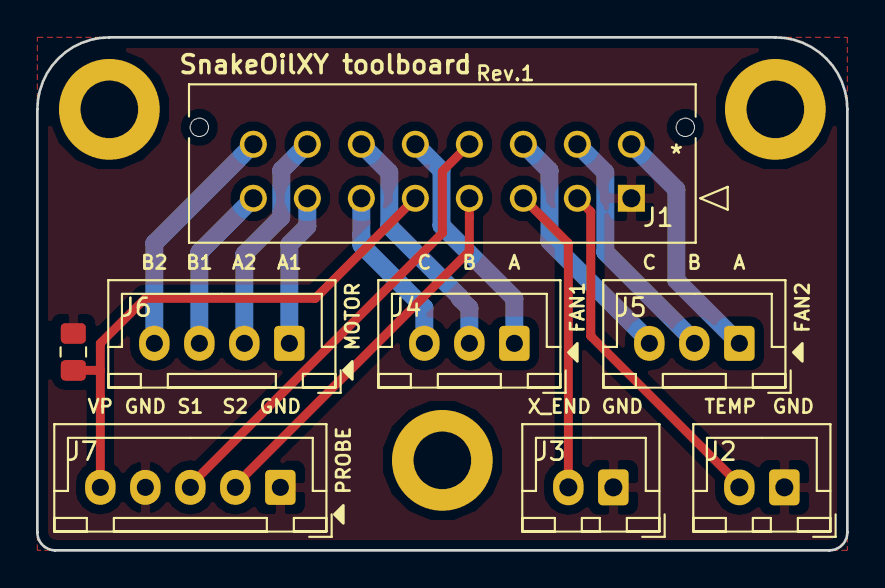
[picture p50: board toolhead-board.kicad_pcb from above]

Board: 2 copper layers, 45.0 x 28.5 mm, 8 parts (0 on the bottom side), 16 nets.

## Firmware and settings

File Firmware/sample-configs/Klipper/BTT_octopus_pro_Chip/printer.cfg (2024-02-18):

# Gcode and custom macros
[include macro.cfg]

# Custom LCD menu, enabe if have mini 12864LCD
#[include menu.cfg]
#[include display.cfg]

# change the b
[mcu]
# USB
serial: /dev/serial/by-id/YOUR_BOARD_ID_HERE
# UART
#serial: /dev/ttyAMA0
#restart_method: command

[force_move]
enable_force_move: False

[printer]
kinematics: corexy
max_velocity: 300 ; 500 or 600 for 48v driver
max_accel: 15000
#max_accel_to_decel: 15000
max_z_velocity: 24
max_z_accel: 240
square_corner_velocity: 5

# motor 0 port
[stepper_x]
step_pin: PF13
dir_pin: !PF12
enable_pin: !PF14
microsteps: 16
rotation_distance: 40
full_steps_per_rotation:400 
endstop_pin: PG15
position_endstop: 182 # 252 for 250 machine
position_max: 182 # 252 for 250 machine
position_min : -5
homing_speed: 50

# [tmc2209 stepper_x]
# uart_pin: PC4
# run_current: 0.800
# hold_current: 0.500
# sense_resistor: 0.110
# interpolate: true
# stealthchop_threshold: 0

[tmc5160 stepper_x]
cs_pin: PC4
spi_software_mosi_pin: PA7
spi_software_miso_pin: PA6
spi_software_sclk_pin: PA5
interpolate: true
run_current: 0.800
# hold_current: 0.500
stealthchop_threshold: 0


# motor 1 port
[stepper_y]
step_pin: PG0
dir_pin: !PG1
enable_pin: !PF15
microsteps: 16
rotation_distance: 40
full_steps_per_rotation:400 
endstop_pin: PG14
position_endstop: 202 # 247 for 250 machine
position_max: 202 # 247 for 250 machine
position_min : 0 # -5 for 250 machine
homing_speed: 50

# [tmc2209 stepper_y]
# uart_pin: PD11
# run_current: 0.800
# hold_current: 0.500
# sense_resistor: 0.110
# interpolate: true
# stealthchop_threshold: 0

[tmc5160 stepper_y]
cs_pin: PD11
spi_software_mosi_pin: PA7
spi_software_miso_pin: PA6
spi_software_sclk_pin: PA5
interpolate: true
run_current: 0.800
# hold_current: 0.500
stealthchop_threshold: 0


# motor 2 port
#[stepper_unused1]
#step_pin: PF11
#dir_pin: PG3
#enable_pin: !PG5
#microsteps: 16
#rotation_distance: 8
#endstop_pin: PG10
#position_endstop: 0
#position_max: 200
#homing_speed: 12
#second_homing_speed: 1

#[tmc2209 stepper_unused1]
#uart_pin: PC6
#interpolate: true
#run_current: 0.800
#hold_current: 0.500
#stealthchop_threshold: 0

#[tmc5160 stepper_unused1]
#cs_pin: PC6
#spi_software_mosi_pin: PA7
#spi_software_miso_pin: PA6
#spi_software_sclk_pin: PA5
#interpolate: true
#run_current: 0.800
#hold_current: 0.500
#stealthchop_threshold: 0


# motor 3 port
[extruder]
step_pin: PG4
dir_pin: PC1
enable_pin: !PA0
rotation_distance: 22.67895
gear_ratio: 5:1
microsteps: 16
full_steps_per_rotation: 200
nozzle_diameter: 0.400
filament_diameter: 1.750
max_extrude_only_distance: 1400.0
max_extrude_only_velocity: 75.0
max_extrude_only_accel: 1500
min_temp: 0
max_temp: 385
max_power: 1.0
min_extrude_temp: 170
smooth_time: 2.0
heater_pin: PB11 # HE3
#sensor_pin:  PF3 # T0
#sensor_type: PT1000
#pullup_resistor: 1000
sensor_type: MAX31865
sensor_pin: PF8
spi_software_sclk_pin: PA5
spi_software_mosi_pin: PA7
spi_software_miso_pin: PA6
rtd_nominal_r: 1000
rtd_reference_r: 4300
rtd_num_of_wires: 2
#rtd_use_50Hz_filter: False
#control: pid
#pid_Kp: 22.2
#pid_Ki: 1.08
#pid_Kd: 114

# [tmc2209 extruder]
# uart_pin: PC7
# run_current: 0.250
# hold_current: 0.150
# sense_resistor: 0.110
# interpolate: true
# stealthchop_threshold: 0

[tmc5160 extruder]
cs_pin: PC7
spi_software_mosi_pin: PA7
spi_software_miso_pin: PA6
spi_software_sclk_pin: PA5
interpolate: true
run_current: 0.250
hold_current: 0.150
stealthchop_threshold: 0


# motor 4 port
#[stepper_unused2]
#step_pin: PF9
#dir_pin: PF10
#enable_pin: !PG2
#microsteps: 16
#rotation_distance: 8
#endstop_pin: PG10
#position_endstop: 0
#position_max: 200
#homing_speed: 12
#second_homing_speed: 1

#[tmc2209 stepper_unused2]
#uart_pin: PF2
#interpolate: true
#run_current: 0.800
#hold_current: 0.500
#stealthchop_threshold: 0

#[tmc5160 stepper_unused2]
#cs_pin: PF2
#spi_software_mosi_pin: PA7
#spi_software_miso_pin: PA6
#spi_software_sclk_pin: PA5
#interpolate: true
#run_current: 0.800
#hold_current: 0.500
#stealthchop_threshold: 0


# motor 5 port
[stepper_z]
step_pin: PC13
dir_pin: !PF0
enable_pin: !PF1
rotation_distance: 40
gear_ratio: 80:16
microsteps: 16
full_steps_per_rotation:400 
endstop_pin: probe:z_virtual_endstop
position_max: 185
position_min: -10
homing_speed: 8
second_homing_speed: 3
homing_retract_dist: 3

[tmc2209 stepper_z]
uart_pin: PE4
run_current: 0.600
# hold_current: 0.450
sense_resistor: 0.110
interpolate: true
stealthchop_threshold: 0

#[tmc5160 stepper_z]
#cs_pin: PE4
#spi_software_mosi_pin: PA7
#spi_software_miso_pin: PA6
#spi_software_sclk_pin: PA5
#interpolate: true
#run_current: 0.600
#hold_current: 0.450
#stealthchop_threshold: 0

# motor 6 port
[stepper_z1]
step_pin: PE2
dir_pin: PE3
enable_pin: !PD4
rotation_distance: 40
gear_ratio: 80:16
microsteps: 16
full_steps_per_rotation:400 

[tmc2209 stepper_z1]
uart_pin: PE1
run_current: 0.600
# hold_current: 0.450
sense_resistor: 0.110
interpolate: true
stealthchop_threshold: 0

#[tmc5160 stepper_z1]
#cs_pin: PE1
#spi_software_mosi_pin: PA7
#spi_software_miso_pin: PA6
#spi_software_sclk_pin: PA5
#interpolate: true
#run_current: 0.600
#hold_current: 0.450
#stealthchop_threshold: 0


# motor 7 port
[stepper_z2]
step_pin: PE6
dir_pin: PA14
enable_pin: !PE0
rotation_distance: 40
gear_ratio: 80:16
microsteps: 16
full_steps_per_rotation:400 

[tmc2209 stepper_z2]
uart_pin: PD3
run_current: 0.600
# hold_current: 0.450
sense_resistor: 0.110
interpolate: true
stealthchop_threshold: 0

#[tmc5160 stepper_z2]
#cs_pin: PD3
#spi_software_mosi_pin: PA7
#spi_software_miso_pin: PA6
#spi_software_sclk_pin: PA5
#interpolate: true
#run_current: 0.600
#hold_current: 0.450
#stealthchop_threshold: 0


[bltouch]
sensor_pin: ^PB7
control_pin: PB6
stow_on_each_sample: False
probe_with_touch_mode: True
x_offset: -28
y_offset: -21
z_offset: 1.800
speed: 10 ;8
sample_retract_dist: 3
samples_result: median
samples: 4

[safe_z_home]
home_xy_position: 90,90 # 125, 120 for 250 machine
speed: 50
z_hop: 15                 # Move up 15mm
z_hop_speed: 5

[z_tilt]
# the point of the motor (or leadscrew - 180 machine)
z_positions:
	210, 90
	-30, 5 
	-30, 175
# the point of the motor (or leadscrew - 250 machine)
# z_positions:
# 	280, 120
# 	-30, 5
# 	-30,235
# probe point (nozzle) / X shift 30, y shift 5 (180 machine)
points:
	175, 110
	55, 30
	55, 190
# probe point (nozzle) / X shift 30, y shift 5 (250 machine)
# points:
	# 245, 135
	# 55, 30
	# 55, 240
speed: 150
horizontal_move_z: 15
retries: 5
retry_tolerance: 0.0075

[bed_mesh]
speed: 50
horizontal_move_z: 10
mesh_min: 0,0 # prob pos
mesh_max: 150, 180 # prob pos (180 machine)
# mesh_max: 220, 230 # prob pos (250 machine)
probe_count: 6,6

[heater_bed]
heater_pin: PA1
sensor_pin: PF7 # T3
sensor_type: NTC 100K beta 3950
#control: pid
min_temp: 0
max_temp: 150
max_power: 0.8
min_temp: 0
#pid_kp: 58.437
#pid_ki: 2.347
#pid_kd: 363.769

##	Hotend Fan --> FAN5
[heater_fan hotend_fan]
pin: PD15
max_power: 1.0
kick_start_time: 0.5
heater: extruder
heater_temp: 50.0
#off_below: 0.25

##	Part Cooling Fan --> FAN4
[fan]
pin: PD14
kick_start_time: 0.5
#off_below: 0.25

# filter fan --> FAN3
[fan_generic filter_fan]
kick_start_time: 0.5
#hardware_pwm: True
pin: PD13

# bed fan --> FAN2
[fan_generic bed_fan] 
kick_start_time: 1
pin: PD12

# bed fan --> FAN1
[fan_generic assist_fan] 
kick_start_time: 1
pin: PE5

# bed fan --> FAN0
[fan_generic test_fan] 
kick_start_time: 1
cycle_time: 0.005
#hardware_pwm: True
max_power: 0.5
pin: PA8

##	mini12864 LCD Display
[display]
lcd_type: uc1701
cs_pin: PE9
a0_pin: PE10
rst_pin: PE12
encoder_pins: ^PB1, ^PB2
click_pin: ^!PE7
contrast: 63
spi_software_miso_pin: PA6
spi_software_mosi_pin: PA7
spi_software_sclk_pin: PA5
menu_timeout: 300
menu_reverse_navigation:false
menu_root: __menutree
display_group: _custom_12864_16x4

##	mini12864 LCD backlight
[neopixel lcd_led]
pin: PE13
chain_count: 3
initial_RED: 1.0
initial_GREEN: 1.0
initial_BLUE: 0.5
color_order: RGB

##	mini12864 LCD beeper
[output_pin BEEPER_pin]
pin: PE8
pwm: True
value: 0
shutdown_value: 0
cycle_time: 0.001
scale: 1000

[neopixel led]
pin: PB0
chain_count: 20
initial_RED: 0.6
initial_GREEN: 1.0
initial_BLUE: 1.0

[temperature_sensor chamber]
sensor_pin: PF6 # T2
sensor_type: NTC 100K beta 3950

[temperature_sensor chamber2]
sensor_type: LM75
i2c_address: 72 # up to 79
#i2c_mcu:
i2c_bus: i2c1a
#i2c_speed:
#   See the "common I2C settings" section for a description of the
#   above parameters.
lm75_report_time: 10 # 0.8

[gcode_button BUTTON3]
pin: ^!PG11
press_gcode:
	TOGGLE_LED

[gcode_button BUTTON2]
pin: ^!PG10
press_gcode:
	PRINT MSG="BTN2"

[gcode_button BUTTON1]
pin: ^!PG9
press_gcode:
	PRINT MSG="BTN1"

[virtual_sdcard]
path: ~/gcode_files


[pause_resume]
recover_velocity: 50


[display_status]

[idle_timeout]
timeout: 1800
gcode:
  UPDATE_DELAYED_GCODE ID=POWER_DOWN DURATION=1 ; call auto power down after print done or canceled


[respond]
# enable M118 and RESPONSE command


# [mcu rpi]
# serial: /tmp/klipper_host_mcu

# [adxl345]
# cs_pin: rpi:None
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

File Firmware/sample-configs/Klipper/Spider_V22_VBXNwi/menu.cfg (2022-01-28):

# This file defines the default layout of the printer's menu.

# It is not necessary to edit this file to change the menu. Instead,
# one may override any of the sections defined here by defining a
# section with the same name in the main printer.cfg config file.

### DEFAULT MENU ###
# Main
#   + Tune
#       + Speed: 000%
#       + Flow: 000%
#       + Offset Z:00.00
#   + SD Card
#       + Start
#       + Resume
#       + Pause
#       + Abort
#       + ... (files)
#   + Motion
#       + Home All
#       + Home Z
#       + Home X/Y
#       + Move
#          + Move 10mm
#               + Move X:000.0
#               + Move Y:000.0
#               + Move Z:000.0
#               + Move E:+000.0
#          + Move 1mm
#               + Move X:000.0
#               + Move Y:000.0
#               + Move Z:000.0
#               + Move E:+000.0
#          + Move 0.1mm
#               + Move X:000.0
#               + Move Y:000.0
#               + Move Z:000.0
#               + Move E:+000.0
#       + Steppers off
#   + Cooling
#       + Layer fan
#       + Bed fan
#       + Filter fan
#   + Temperature
#       + Cooldown
#           + Cooldown all
#           + Cooldown hotend
#           + Cooldown hotbed
#       + Ex0:000 (0000)
#       + Ex1:000 (0000)
#       + Bed:000 (0000)
#       + Preheat PLA
#           + Preheat all
#           + Preheat hotend
#           + Preheat hotbed
#       + Preheat PETG
#           + Preheat all
#           + Preheat hotend
#           + Preheat hotbed
#       + Preheat ABS
#           + Preheat all
#           + Preheat hotend
#           + Preheat hotbed
#   + Filament
#       + Ex0:000 (0000)
#       + Load Fil.
#       + Unload Fil.
#       + Feed: 000.0
#       + Cooldown
#   + Setup
#       + Auto align Z
#       + Bed mesh
#       + Probe calibrate
#           + Start calibrate
#           + Adjust Z ++
#           + Accept
#           + Abort
#       + Apply gcode offset
#       + Probe acc. test
#       + PID tuning
#           + Tune Hotend PID
#           + Tune Hotbed PID
#       + Save(restart)
#       + Save(pending)
#       + Dump parameters
#       + Restart
#           + Restart host
#           + Restart FW

### menu main ###
[menu __menutree]
type: list
name: Main

### menu tune ###
[menu __menutree __tune]
type: list
enable: {printer.idle_timeout.state == "Printing"}
name: Tune

[menu __menutree __tune __speed]
type: input
name: Speed: {'%3d' % (menu.input*100)}%
input: {printer.gcode_move.speed_factor}
input_min: 0
input_max: 5
input_step: 0.05
realtime: True
gcode:
    M220 S{'%d' % (menu.input*100)}

[menu __menutree __tune __flow]
type: input
name: Flow: {'%3d' % (menu.input*100)}%
input: {printer.gcode_move.extrude_factor}
input_min: 0
input_max: 2
input_step: 0.01
realtime: True
gcode:
    M221 S{'%d' % (menu.input*100)}

[menu __menutree __tune __offsetz]
type: input
name: Offset Z:{'%05.3f' % menu.input}
input: {printer.gcode_move.homing_origin.z}
input_min: -5
input_max: 5
input_step: 0.025
realtime: True
gcode:
    SET_GCODE_OFFSET Z={'%.3f' % menu.input} MOVE=1

### menu virtual sdcard ###
[menu __menutree __sdcard]
type: vsdlist
enable: {('virtual_sdcard' in printer)}
name: SD Card

[menu __menutree __sdcard __start]
type: command
enable: {('virtual_sdcard' in printer) and (printer.print_stats.state == "standby" or printer.print_stats.state == "error" or printer.print_stats.state == "complete")}
name: Start
gcode:
    { menu.exit(True) }
    PLAY_SINGLE_FEEDBACK_SOUND
    M24

[menu __menutree __sdcard __resume]
type: command
enable: {('virtual_sdcard' in printer) and printer.print_stats.state == "paused"}
name: Resume
gcode:
    { menu.exit(True) }
    PLAY_SINGLE_FEEDBACK_SOUND
    RESUME

[menu __menutree __sdcard __pause]
type: command
enable: {('virtual_sdcard' in printer) and printer.print_stats.state == "printing"}
name: Pause
gcode:
    PLAY_SINGLE_FEEDBACK_SOUND
    { menu.exit(True) }
    PAUSE

[menu __menutree __sdcard __abort]
type: command
enable: {('virtual_sdcard' in printer) and (printer.print_stats.state == "printing" or printer.print_stats.state == "paused")}
name: Abort
gcode:
    { menu.exit(True) }
    CLEAR_PAUSE
    CANCEL_PRINT
    SDCARD_RESET_FILE

### menu control ###
[menu __menutree __motion]
type: list
name: Motion

[menu __menutree __motion __home]
type: list
name: Home

[menu __menutree __motion __home __homeall]
type: command
enable: {not printer.idle_timeout.state == "Printing"}
name: Home All
gcode:
    PRINT MSG="Homing..."
    G28
    PRINT MSG="Ready"


[menu __menutree __motion __home __homexy]
type: command
enable: {not printer.idle_timeout.state == "Printing"}
name: Home X/Y
gcode:
    PRINT MSG="XY Homing..."
    G28 X Y
    PRINT MSG="Ready"

[menu __menutree __motion __home __homez]
type: command
enable: {not printer.idle_timeout.state == "Printing"}
name: Home Z
gcode:
    PRINT MSG="Z Homing..."
    G28 Z
    PRINT MSG="Ready"
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

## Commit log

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2021-06-12 added bottom electronic panel
    [WAGO 221-413.STEP, bottom-panel-assembly.FCStd]
2021-06-13 added electromic and panel mount
    [PSU-LRS-150-din-mount.FCStd, PSU-RS-25.FCStd, back-inner-din-end.FCStd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]
2021-06-17 added sensor and panel mount
    [180-bed-assembly.FCStd, 2020-tslot.FCStd, 3030-alpha-extrusion-joiner.FCStd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]
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2021-06-22 Fixed magnet quantity(BOM)
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2021-06-29 update BOM, change files layout
    [180-bed-assembly.FCStd, 2020-bracket.FCStd, 2020-tslot.FCStd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]
2021-06-29 update door assembly, BOM
    [front-panel-assembly.FCStd, sliding-door.FCStd]
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2021-06-30 update CAD,BOM, bed drawing
    [180-bed-assembly.FCStd, z-arm.FCStd]
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2021-07-08 update BOM, front idler
    [front-idler-assembly.FCStd, left-idler.FCStd, right-idler.FCStd]
2021-07-10 update Z motor mount, z block mount
    [180-bed-assembly.FCStd, 80t-gearbox.FCStd, z-arm.FCStd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]
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2021-07-13 update AB motor mounts
    [front-idler-spacer.stl, left-motor-assembly.FCStd, motor-mount-common.FCStd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]
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2021-07-17 fixed z-motor-cap
    [80t-gearbox.FCStd, z-motor-left-assembly.FCStd, z-motor-right-assembly.FCStd]
2021-07-18 update bottom-panel, fixed z idler housing
    [bottom-panel-assembly.FCStd, z-diler-assembly.FCStd, z-idler.FCStd]
2021-07-18 fixed y carrier
    [y-carrier-left-alt.FCStd, y-carrier-left-assembly.FCStd, y-carrier-right-alt.FCStd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]
2021-07-18 fixed corupted file
    [y-carrier-left-alt.FCStd, y-carrier-left-assembly.FCStd]
2021-07-19 update z belt mounter
    [z-arm.FCStd, z-belt-mounter-assembly.FCStd]
2021-07-20 fixed x-endstop
    [endstop.FCStd, rail-aligner-wider.FCStd]
2021-07-21 update y carrier, din mount
    [back-panel-assembly.FCStd, back-panel-dien-alt.FCStd, din-rail-cutter.stl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]
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2021-07-21 fix z-idler
    [z-arm-mod.FCStd, z-diler-assembly.FCStd, z-idler-assembly.FCStd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]
2021-07-22 fixed motor cover plate
    [80t-gearbox.FCStd, bottom-panel-assembly.FCStd, bottom-panel-template.step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]
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2021-07-26 update bottom panel, z motor cover
    [80t-gearbox.FCStd, bottom-panel-assembly.FCStd, z-motor-left-assembly.FCStd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]
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2021-08-04 update z idler mount
    [z-idler-assembly.FCStd, z-idler.FCStd]
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2021-08-12 update pane & cable mounter
    [back-top-panel-assembly.FCStd, bltouch-mount-thread-insert-mod.FCStd, dragon-mount-thread-insert-mod.FCStd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]
2021-08-13 added AD socket mounter
    [ac-plug.FCStd]
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2021-08-20 update Z rail mounts, BOM
    [180-bed-assembly.FCStd, LCD-assembly.FCStd, LCD-mount.FCStd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]
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2021-08-22 update air filter, added spool holder
    [air-filter-4010-blower.FCStd, air-filter-assembly.FCStd, filament-spool-holder-assembly.FCStd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]
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2021-09-01 added missing STL, update Readme.md
    [4x_foot.stl]
2021-09-05 add top lid, updat BOM
    [1x_lid-left-bottom-hinge.stl, 1x_lid-left-top-hinge.stl, 1x_lid-right-bottom-hinge.stl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]
2021-09-06 added 250x240x230 frame bom
    [filament-guide.FCStd]
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2021-09-25 update link for camera
    [sliding-door-simple.FCStd]
2021-10-02 fixed bom
    [front-panel-assembly.FCStd, sliding-door-simple.FCStd]
2021-10-02 fixed bom - again
2021-10-05 added document for EVA2
    [1x_extruder-bottom-plate.stl, 1x_extruder-motor-support_sherpa-mini.stl, 1x_extruder-top-plate_sherpa-mini.stl]
2021-10-07 update STEP, front panel mount
    [1x_filament-guide-e3d-collet.stl, 2x_door-magnet-mount-large.stl, 2x_door-magnet-mount-small.stl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]
2021-10-08 update CAD, new STL
    [12x_mounter-inner.stl, 12x_mounter-outer.stl, 1x_door-magnet-mount-large.stl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]
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2021-10-15 fixed extrusion length of 250 frame
    [1x_z-rail-block-mount-right-with-limiter.stl, y-carrier-cf.FCStd, z-arm.FCStd]
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2021-10-24 Z rail block with limiter by default
    [1x_z-rail-block-mount-right-no-limiter.stl, 1x_z-rail-block-mount-right-with-limiter.stl, 2x_z-rail-block-mount-left-no-limiter.stl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]
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2021-10-28 update BOM, added option for threaded ball bed coupler
    [1x_back-left-arm.stl, 1x_front-left-arm.stl, 1x_middle-right-arm.stl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]
2021-10-30 update BOM for threaded ball coupler
    [1x_back-left-arm.stl, 1x_extruder-back-plate.stl, 1x_extruder-front-plate.stl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]
2021-11-01 added din cable mounter stl
    [optional_din-cable-mounter.stl]
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2021-11-03 added missing stls
    [1x_bottom-plate.stl]
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2021-11-07 added missing stl
    [2x_ab-motor-spacer.stl, 4x_front-idler-spacer.stl, 4x_idler-spacer.stl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]
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2021-11-11 - Update silicon heater drawing - Add printable 80t pulley by Charles - sync wip assembly
    [80T-gear-replacement_v3_Charles.step, aluminum-bed.FCStd, bed-assembly.FCStd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]
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2021-11-11 Added logos, fixed BOM redirects.
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2021-11-13 fixed broken link
    [bed-assembly.FCStd, v1-180-assembly.FCStd]
2021-11-13 fixed assembly
    [front-idler-assembly.FCStd, v1-180-assembly.FCStd, y-carrier-left-1515-assembly.FCStd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]
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2021-11-18 fixed parts name in assembly
    [LCD-assembly.FCStd, toolhead-carrier-sherpa-1515-assembly.FCStd, v1-180-assembly.FCStd]
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2021-11-30 fix STLs orientation
    [12x_z-motor-spacer.stl, 1x_5v-psu-din--bottom-mount-alt.stl, 1x_air-filter-body.stl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]
2021-12-01 update 1515 bed cable mounter, added cherrymx button cap template
    [1x_bed-cable-mounter.stl, 1x_cherry-mx-mounter.stl, 1x_cherrymx-mounter.stl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]
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2021-12-12 fixed stl orientation
    [1x_top-right-cover.stl, 2x_bottom-left-cover.stl, 2x_top-left-cover.stl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]
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2021-12-14 Z axis gear box : Improvement cable management
    [1x_z-motor-top-plate-right.stl, 2x_z-motor-top-plate-left.stl, 80t-gearbox.FCStd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]
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2021-12-25 hollow out unned parts of toolhead back plate
    [1x_extruder-back-plate.stl, fund.csv, toolhead-carrier-sherpa-1515-assembly.FCStd]
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2021-12-31 update documents, add STL for extrusion drilling tool
    [OPTIONAL_wago-5x1.stl, din-rail-cutter.stl, drilling-jig.FCStd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]
2022-01-01 fixed gasket and din mount
    [1x_bottom-cable-mounter.stl, 250_MACHINE_ONLY_2x_gasket-50mm-extend.stl, 250_MACHINE_ONLY_2x_gasket-70mm-extend.stl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]
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2022-01-03 update BOM, add patch for Z rail block mount
    [1x_z-rail-block-mount-right-with-limiter.stl, 2x_z-rail-block-mount-left-with-limiter.stl, 80t-gearbox-old.FCStd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]
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2022-01-03 fix Z block mount
    [1x_z-rail-block-mount-right-with-limiter.stl, 2x_z-rail-block-mount-left-with-limiter.stl, ALT_1x_z-rail-block-mount-right-with-limiter-dual.stl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]
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2022-01-04 Fix various typos
    Found via `codespell -q 3`
    [fund.csv, macro.cfg, menu.cfg]
2022-01-05 Fix typo in source
    [menu.cfg]
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2022-01-10 fixed panel mount
    [1x_bottom-left-corner-mount.stl, 1x_bottom-right-corner-mount.stl, 1x_cherrymx-mounter.stl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]
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2022-01-22 fix 120mm fan mounter
    [2x_120mm-fan-mounter-mirror_for-250-machine.stl, 2x_120mm-fan-mounter_for-250-machine.stl, ac-bed-connector.FCStd]
2022-01-23 fixed stl
    [1x_left-idler-bottom.stl, 1x_left-idler-mid.stl, 1x_left-idler-top.stl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]
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2022-02-01 Added Tensioning Idlers in Mod folder. Reorganized the folder structure in the STLs section. Combined the tools folder and tools folder in stls folder. Added recommended to the default optoins when a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
    [12x_mounter-inner.stl, 12x_mounter-outer.stl, 17x_panel-mounter.stl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]
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2022-02-02 update neopixel mount, reinforce Z motor mount
    [1x_z-motor-body-right.stl, 2x_neopixel-arm-rev.stl, 2x_neopixel-arm.stl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]
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2022-02-02 fixed STLs orientation
    [OPTIONAL_panel-mounter-with-offset-rev.stl, OPTIONAL_panel-mounter-with-offset.stl]
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2022-02-19 added missing cutout on Z motor mount
    [1x_z-motor-back-plate-right.stl, 1x_z-motor-body-right.stl, 1x_z-motor-top-plate-right.stl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]
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2022-05-22 Fixed english mistakes in the reasonance tuning guide
    [4x_foot_insert_TPU.stl]
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2022-10-25 removed M5 thread insert from idex motor mount
    [idex-motor-mount.FCStd]
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2023-01-10 added 120mm fan mount for 2020-250 bed frame
    [2x_120mm-fan-mounter-_for-250-machine.stl, 2x_120mm-fan-mounter-mirror_for-250-machine.stl, bed-fan-mounter-2020-250.FCStd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]
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2023-04-16 Squashed commit of the following:
    - add code for adding part colors to STL file names
    - rename ambiguous CAD components and STL files to match
    [1x_can-pcb-mounter-cable-guide.stl, 4PR-assembly.FCStd, toolhead-sherpa-pcb-1515-assembly.FCStd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]
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2023-12-28 update IDEX bottom and back plate(use instert instead of hex nut)
    [1x_idex_back_plate_left.stl, 1x_idex_back_plate_right.stl, 2x_extruder_bottom_plate.stl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]
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2024-05-04 add 4PR+4FR reinforce STLs
    [4PR-motor-aligner.FCStd, A_2x_c-belt-mounter-bottom.stl, A_2x_c-motor-shaft-spacer.stl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]
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2025-02-05 Update bom-IDEX.md
    No longer available.
2025-02-05 Update bom-250.md, mellow kit no longer available.
2025-02-05 Update bom-180.md, mellow kit no longer available.

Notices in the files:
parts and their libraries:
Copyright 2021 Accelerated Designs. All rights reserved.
